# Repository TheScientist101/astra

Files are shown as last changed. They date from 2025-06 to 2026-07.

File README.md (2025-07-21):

<h1 align="center">astra</h1>

   

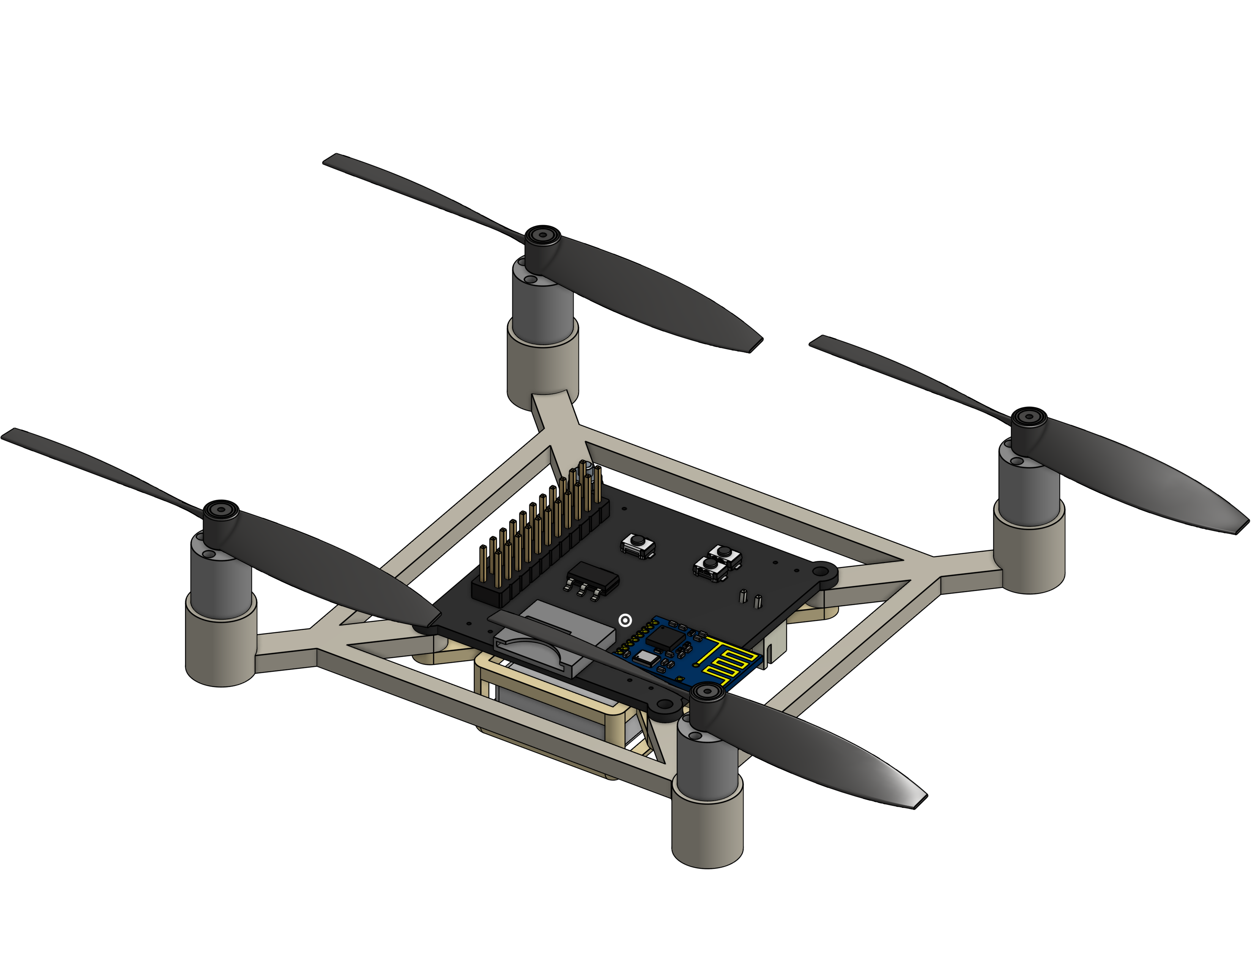
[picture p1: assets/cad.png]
Drone
<h3 align="center">An open source, low cost, extensible brushed drone.</h3>

## What is Astra?

Astra is an `~80mm` brushed quadcopter. It it powered off of a single 1s Li-Po (`4.2V`), and uses four brushed motors.

Astra supports an optional FPV module, and includes a HAT-style pin interface on the flight controller.

We've also designed our own transmitter for Astra. The flight controller and transmitter use an `nRF24` to communicate with low latency.

Every part of Astra was designed from scratch - the flight controller, the transmitter, and the frame.

## Why is Astra?

Siddhant and I both love making things, but we've never made anything that moves before. What cooler of a thing is there that moves than a drone? With air voyage in our control, it would open the gate to even cooler projects, like imagine if you could play laser tag with a drone as your teammate or if you could have a drone that follows you around and takes pictures of you. The possibilities are endless!

That's why we decided to make our drone extensible. To me, modularity is the coolest part of any gadget. It allows you to add new features and capabilities without having to redesign the entire thing. Astra has a HAT-style pin interface called the DUCKDUCKGOOSE (Digital Unified Centralized Kibibit Device Universal Coding Knowledge Generic Operable Objective Service Extensible) Connector on the flight controller, which allows you to add new peripherals and sensors easily.

On the other hand, most drone projects we've seen online are expensive. While Hack Club is dope enough to have a [program that gives us free hardware](https://highway.hackclub.com), it is difficult to find a "DIY" drone that is relatively cheap that flies well. Since we wanted to make sure that our drone was actually good at flying, we decided to remove the onboard camera that we had in our initial design in place of a more traditional FPV system rather than just trying to make our own.

## Cost

All of the components for the drone and can be bought for around `$75`. (See the [`BOM`](./BOM.md) for more details!)

The bulk of this is actually the cost to buy the PCBs and stencil (which is anticipated to be around `$25`). The actual component cost is closer to `$50`.

> Note:
> Adding an FPV system to the drone is relatively costly. The FPV Camera + VTX module costs `$25`, which is actually on the cheaper end for these systems. The total cost with the FPV module is slightly less than `$100` before taxes and other fees.

(for hackclub) Even though the total cost of this drone is under `$150`, we will likely need to have multiple iterations of the PCB before we can get it working right.

## Technical Details

The Flight Controller uses an `STM32H750`. This is a powerful chip with plenty of GPIO pins for peripherals. We plan to implement a software OSD within the H7 for the FPV interface.

PCB files can be found within the `drone/pcb/` folder.

The Flight Controller uses the [betaflight](https://betaflight.com/) firmware. A betaflight config file as well as flashing instructions can be found in the `drone/firmware/` folder

The frame for the FC was designed in Onshape. CAD files can be found in `drone/cad/`;

**Peripherals**:

- `BMI270` - IMU
- `BMP388` - Barometer
- 2 `WS2812B`s
- 2 configurable buttons
- microSD Card Socket
- A 22 pin header for HAT-style extensions. Includes SWD, UART, SPI, I2C, and extra GPIOs.
- An extra UART connector.

The Ground Transmitter uses an `ESP32-C3-SuperMini` (a C3 chip similar to the XIAO that we already have on hand). It features:

- 3 `WS2812B`s
- 2 Joysticks, configured for mode 2 control
- 4 configurable buttons (+2 from the joysticks)

The PCB, firmware, and case for the transmitter can be found in the `controller/` folder

## Pictures

[**Full Schematic PDF**](assets/schematic.pdf)

**Copper Layers:**

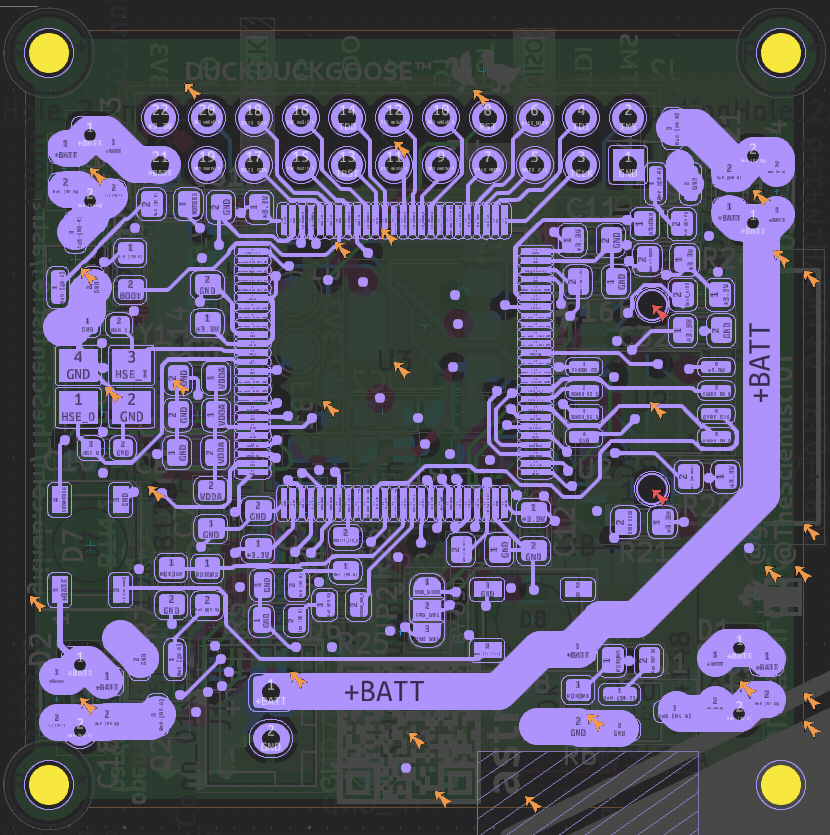
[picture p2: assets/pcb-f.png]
Front Copper Layer
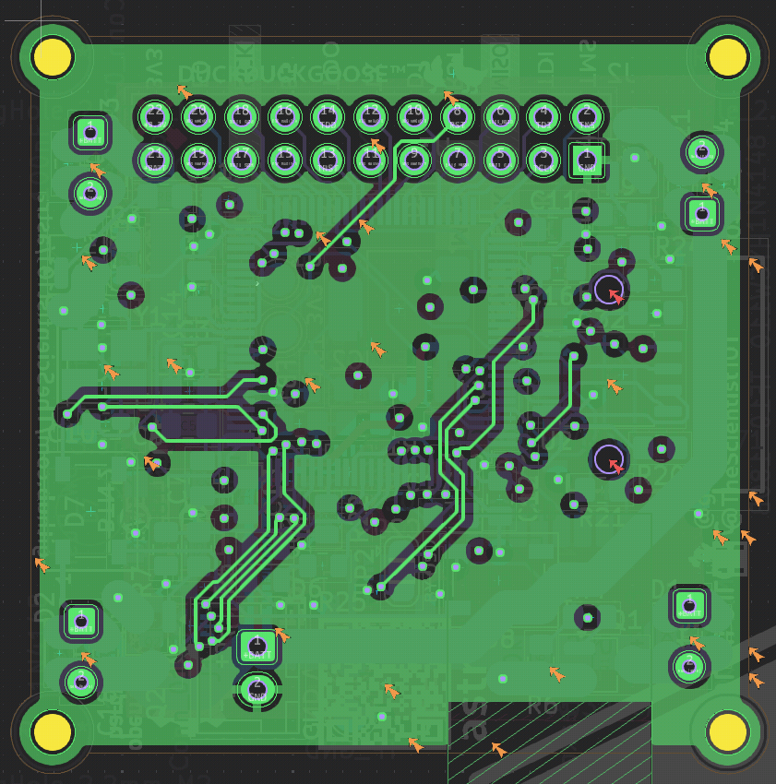
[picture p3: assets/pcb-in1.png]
Inner Layer 1
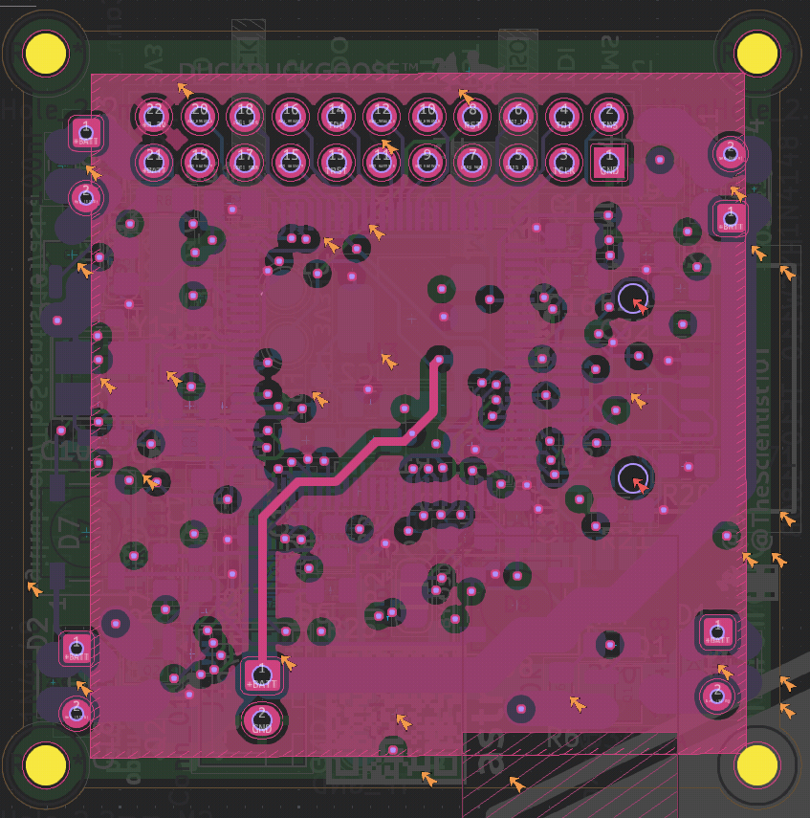
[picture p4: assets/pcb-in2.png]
Inner Layer 2
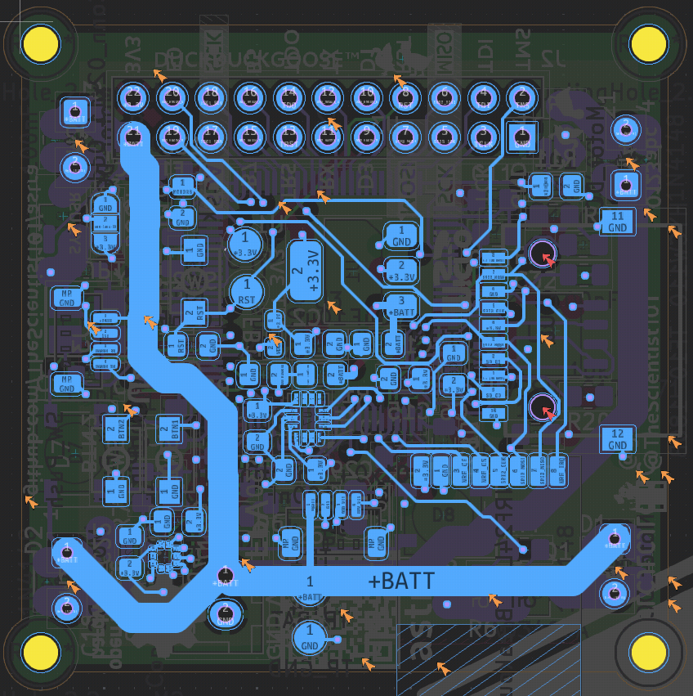
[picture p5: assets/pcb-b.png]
Back Copper Layer
   

**PCB 3D Render:**

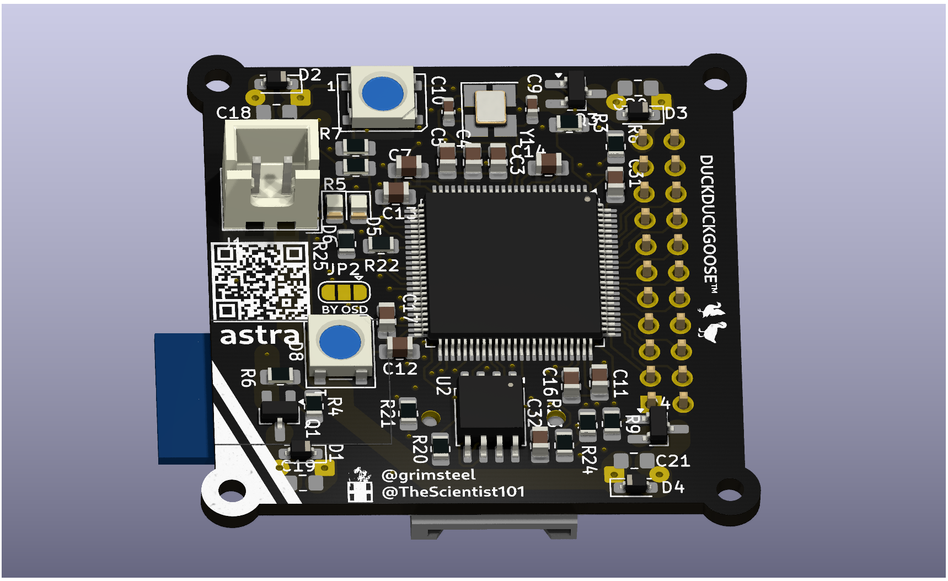
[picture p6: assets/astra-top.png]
top
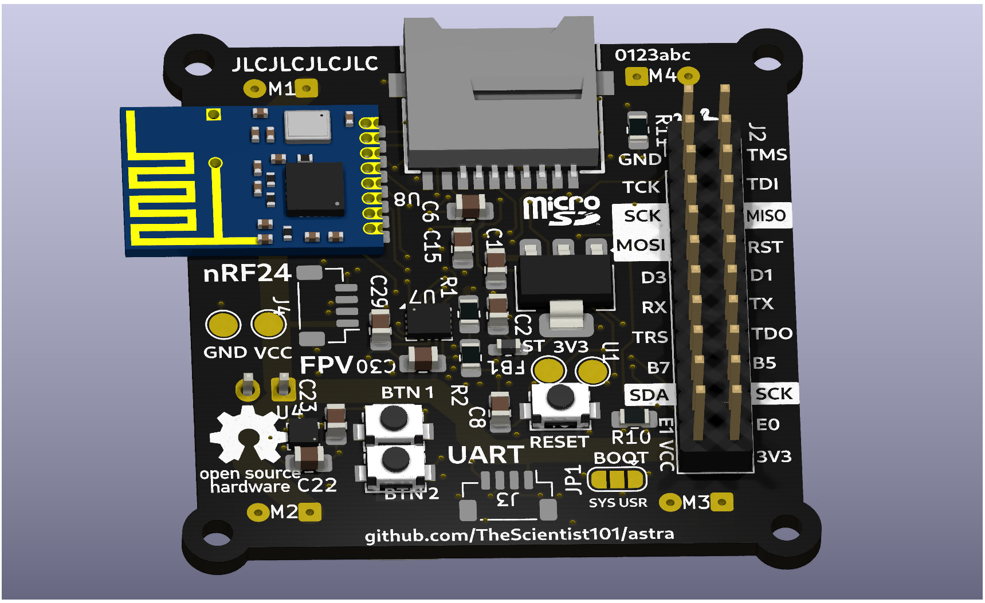
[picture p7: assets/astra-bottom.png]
bottom
 

**Controller PCB Render:**
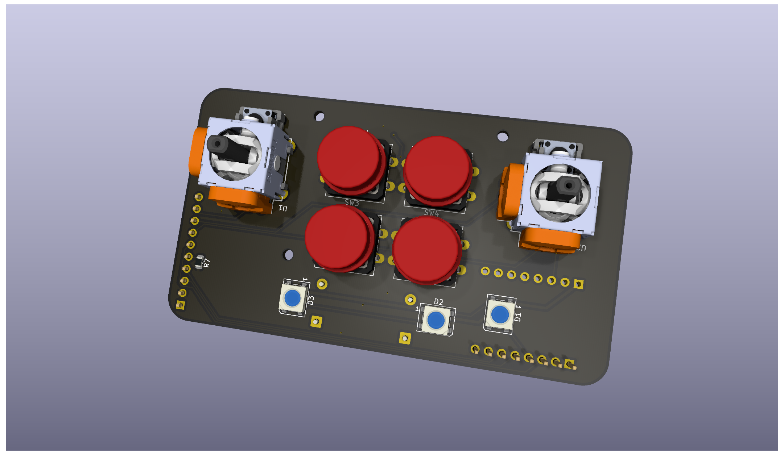
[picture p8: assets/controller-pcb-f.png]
controller pcb front
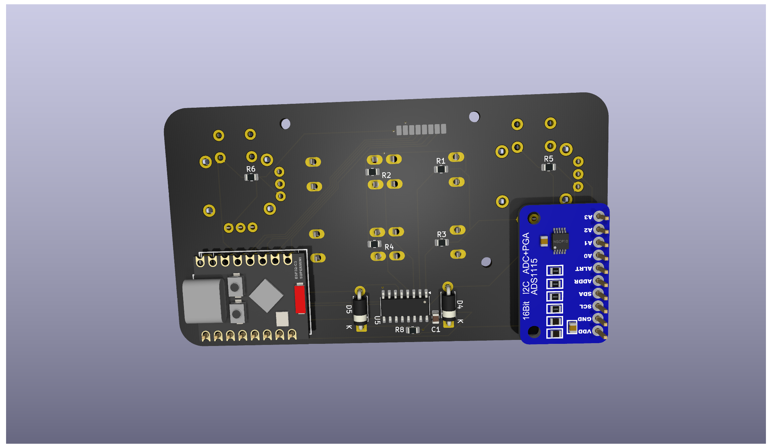
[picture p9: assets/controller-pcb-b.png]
controller pcb back
 

**Controller Assembled Render:**
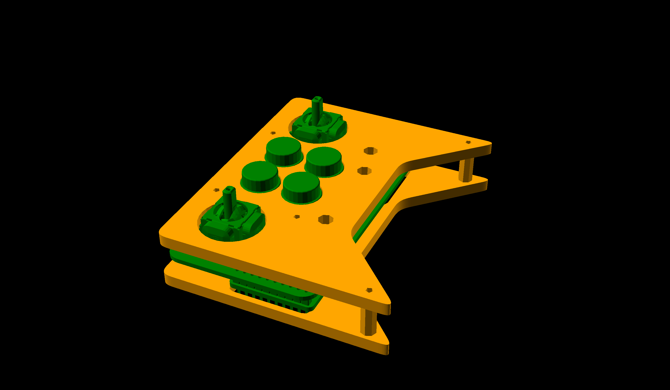
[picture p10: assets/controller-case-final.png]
controller assembled


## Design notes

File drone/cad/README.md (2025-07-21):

# Drone Frame and Battery Holder CAD

The frame and battery holder were designed in Onshape.

[Onshape document](https://cad.onshape.com/documents/556a86aa248807ec932b202d/w/b9d21806660e18ae1fcb018e/e/1638ad71585b5f3276a24b8a)



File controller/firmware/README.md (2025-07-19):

# Ground Controller Firmware

Firmware for the `ESP32-C3-Super Mini` using `esp-idf`.

Drone communication uses the `V202` protocol.

### Credits and Libraries used:

- [`esp-idf-mirf`](https://github.com/nopnop2002/esp-idf-mirf) - nRF24 driver
- [`Flaykz/Wltoys-v202`](https://github.com/Flaykz/Wltoys-v202) - V202 protocol code/TX implementation
- [`betaflight`](https://github.com/betaflight/betaflight/blob/master/src/main/rx/nrf24_v202.c) - Betaflight's V202 implementation (used on the drone)

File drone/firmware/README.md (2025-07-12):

# Building Astra's firmware

Astra's firmware is based on [Betaflight](https://betaflight.com).

We've provided a config in `config.h`. This includes everything except the timer DMA configuration - we need the physical board to figure out this.

Follow these instructions to setup a Betaflight build environment: https://betaflight.com/docs/category/building

## Detailed instructions:

1. Setup Betaflight build environment:
   ```bash
   $ git clone https://github.com/betaflight/betaflight.git
   $ cd betaflight
   $ make arm_sdk_install # if you don't have it installed already
   $ make configs
   ```
   
2. Copy astra config
   ```bash
   $ mkdir -p src/config/configs/ASTRA/
   $ cp /path/to/astra/firmware/config.h src/config/configs/ASTRA/
   ```
   
3. Apply patch to enable nRF24 RX
   ```bash
   $ git apply /path/to/astra/firmware/0001-build-link-NRF24-protocol-sources.patch
   ```
   
4. Build
   ```bash
   $ make ASTRA
   ```

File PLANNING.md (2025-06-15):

# Planning

This is a mirror of our Slack canvas.

## Features

* Parachute
* Solar Panel
    * https://www.aliexpress.us/item/3256808773901038.html
* Toy Ammunition
* Alternate Terrains
* Perching Mechanism
* Autonomous Navigation
    * Auto-Following
        * Using radio signal or camera
        * One follows another
* Mapping using LiDAR or Camera
    * Fastest path
* Radio Integration
* Aerial Laser Tag
* 6“ x 6”

## Budget

Remember to 2x everything at the end

* ESP32-S2 (ESP32-S2-MINI-1U-N4) -  $3.62
    * https://www.digikey.com/en/products/detail/espressif-systems/ESP32-S2-MINI-1U-N4/13180197
* SPI NOR Flash - $0.56
    * BY25Q64ESTIG
* OV3660 or OV2460 - ~$4 - ~10 grams
* Camera Connector - DF40C-30DP-0.4V - $0.81
    * https://www.digikey.com/en/products/detail/hirose-electric-co-ltd/DF40C-30DP-0-4V-51/1969483
* Solder Paste
    * Digikey NC191LT10
    * Aliexpress https://www.aliexpress.us/item/3256806096656294.html $2.98
* PCB - $20-ish - ~10 grams with components except for camera
* Battery - https://www.getfpv.com/sub250-300mah-1s-75c-lipo-battery-5-pcs-a30.html
* IMU - 
* Set of SMD Capacitors/resistors
    * https://www.aliexpress.us/item/3256805970706203.html - 0805 $4.26 for 320pcs
    * https://www.aliexpress.us/item/3256807716137879.html - 0805 $4.17 for 1000pcs (optional)
* AMS1117 3.3
    * Already have
* Propeller
    * https://hackermotors.us/product/gws-prop-3-x-3-hd-set-with-2-pcs/
* Motor ~ 20 grams for all four
    * https://www.aliexpress.us/item/3256802734081484.html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
    * https://excelrc.com/products/betafpv-7x16mm-brushed-motors-19000kv-2cw-2ccw?variant=37534134403259&country=US¤cy=USD&gQT=1
    * https://speedyfpv.com/collections/brushed-motors
    * https://www.amazon.com/Coreless-Brushed-JST-1-25-Connector-Quadcopter/dp/B0CZ6WKVBK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
    * https://www.amazon.com/YoungRC-8520-Coreless-Propeller-Quadcopter/dp/B0BV6P4XYX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—yy_v-cQuJQKe_gynbgR_eZBlEEt8VdUATcRUv22JsLWLuzio.u-IRMGxt2WgfQ5QidPC23q36qNFRAg0-ucyN7Pd-z48&dib_tag=se&keywords=micro+motors&qid=1748056601&s=industrial&sprefix=micro+motors%2Cindustrial%2C121&sr=1-2-spons&sp_csd=d2lkZ2V0TmFtZT1zcF9hdGY&psc=1#averageCustomerReviewsAnchor
* Laser - $6 - ~10 grams
    * https://www.adafruit.com/product/1054
* 3d printing filament ~50 grams

## Motor Math

* Maximum of 150 grams with motors
* at least 75 g of thrust per motor
* 

## Resources

* https://files.seeedstudio.com/wiki/SeeedStudio-XIAO-ESP32S3/res/XIAO_ESP32S3_ExpBoard_v1.0_SCH.pdf
* https://www.unmannedsystemstechnology.com/feature/calculating-how-much-weight-a-drone-can-carry/
* https://www.digikey.com/en/maker/projects/a-step-by-step-guide-to-build-a-low-cost-drone-using-esp32/8afccd0690574bcebfa0d2ad6fd0a391

Measuring battery level: https://vivonomicon.com/2019/10/15/reading-battery-voltage-with-the-stm32s-adc/

OV5640 wiring: https://cdn-learn.adafruit.com/assets/assets/000/118/304/original/adafruit_products_cam_schem.png?1675865865
BMI270 wiring: https://cdn.sparkfun.com/assets/c/a/3/d/f/SparkFun_Qwiic_6DoF_BMI270-Schematic.pdf

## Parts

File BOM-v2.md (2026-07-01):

# Bill of Materials

## General Items and Modules/Breakouts (Amazon + AliExpress)

| Item | Link | Quantity | Total Price | Total Mass on Drone |
|---|---|---|---|---|
| PCB | | 1 | ~$25 | 10g |
| Estimated Tax | - | - | $8.07 | - |
| **Total** | - | - | | |

> The Amazon order total is above $35, so shipping is free.

## PCB Components (LCSC)

_Mass estimate is included in PCB mass estimate_

| Item | Link | Quantity | Total Price | Already Have? |
|---|---|---|---|---|
| ESP32-S3-WROOM-1U-N4R2 | [LCSC](https://www.lcsc.com/product-detail/C3013942.html) | 1 | $4.42 | |
| U.FL Wi-Fi Antenna | [LCSC](https://www.lcsc.com/product-detail/C22467592.html) | 1 | $0.37 | |
| 64 MB NOR Flash: W25Q64JVSSIQ | [LCSC](https://www.lcsc.com/product-detail/NOR-FLASH_Winbond-Elec-W25Q64JVSSIQ_C179171.html?s_z=n_W25Q16JV) | 1 | $0.88 | Yes |
| 32.768 kHz crystal (optional) | [LCSC](https://www.lcsc.com/product-detail/C32346.html) | 1 | $0.87 (5 ct) | |
| TLV1117LV-3.3 | [LCSC](https://lcsc.com/product-detail/Voltage-Regulators-Linear-Low-Drop-Out-LDO-Regulators_JSMSEMI-TLV1117LV33DCYR_C48937499.html) | 1 | $0.54 (for 5) | Yes |
| | | | | |
| A03400A NMOS | [LCSC](https://lcsc.com/product-detail/MOSFETs_UMW-Youtai-Semiconductor-Co-Ltd-AO3400A_C347475.html) | 4 | $0.62 (for 20) | Yes |
| 1N4148 Flyback | [LCSC](https://lcsc.com/product-detail/Switching-Diodes_MDD-Microdiode-Semiconductor-1N4148WS-E_C41371421.html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) | 4 | $0.06 (10 ct) | Yes |
| | | | | |
| 100nF 16V 0805 Capacitor | [LCSC](https://www.lcsc.com/product-detail/Multilayer-Ceramic-Capacitors-MLCC-SMD-SMT_Venkel-C0805X7R160-104KNP_C3865954.html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) | 16 | $0.35 (50 ct) | Yes |
| 1uF 16V 0805 Capacitor | [LCSC](https://www.lcsc.com/product-detail/Multilayer-Ceramic-Capacitors-MLCC-SMD-SMT_Samsung-Electro-Mechanics-CL21B105KOFNNNE_C24123.html) | 2 | $0.21 (20 ct) | Yes |
| 22uF 16V 0805 Capacitor | [LCSC](https://www.lcsc.com/product-detail/C380336.html) | 2 | $0.64 (10 ct) | |
| 5k1 125mW 0603 Resistor | [LCSC](https://www.lcsc.com/product-detail/C23186.html) | 4 | | Yes |
| 1k 125mW 0805 Resistor | [LCSC](https://lcsc.com/product-detail/Chip-Resistor-Surface-Mount_FOJAN-FRC0805J102-TS_C2907295.html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) | 1 | $0.13 (100 ct) | Yes |
| | | | | |
| SD Card Socket | [LCSC](https://lcsc.com/product-detail/SD-Card-Memory-Card-Connector_HOAUC-HYCW110-TF10-180B_C2962030.html) | 1 | $0.54 (10 ct) | Yes |
| SPST Push Button | [LCSC](https://lcsc.com/product-detail/Tactile-Switches_SHOU-HAN-TS342A2P-WZ_C557591.html) | 3 | $0.37 (10 ct) | Yes |
| 0805 Green LED | [LCSC](https://lcsc.com/product-detail/LED-Indication-Discrete_Yongyu-Photoelectric-SZYY0805G1_C19712537.html) | 1 | $0.27 (50 ct) | Yes |
| WS2812B | [LCSC](https://lcsc.com/product-detail/RGB-LEDs-Built-in-IC_XINGLIGHT-XL-5050RGBC-WS2812B-S_C22461793.html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) | 3 | $0.53 (20 ct) | Yes |
| | | | | |
| BMI270 IMU | [LCSC](https://www.lcsc.com/product-detail/Accelerometers_Bosch-Sensortec-BMI270_C2836813.html?s_z=n_BMI270) | 1 | $2.41 (other suppliers) | Soldered |
| QMC5883P Compass | [LCSC](https://www.lcsc.com/product-detail/C2847467.html) | 1 | $1.53 | |
| HBP401G101S6 Barometer | [LCSC](https://www.lcsc.com/product-detail/C49229983.html) | 1 | $0.89 | |
| ATGM332D GPS | [LCSC](https://www.lcsc.com/product-detail/C3037611.html) | 1 | $1.80 | |
| AT2659 LNA | [LCSC](https://www.lcsc.com/product-detail/C883443.html) | 1 | $0.43 (5 ct) | |
| 470 pF 0603 Capacitor | [LCSC](https://www.lcsc.com/product-detail/C3893316.html) | 1 | $0.11 (50 ct) | |
| 6.8 nH 0603 Inductor | [LCSC](https://www.lcsc.com/product-detail/C55067207.html) | 1 | $0.23 (50 ct) | |
| GNSS Patch Antenna | [LCSC](https://www.lcsc.com/product-detail/C6569550.html) | 1 | $0.66 | |
| | | | | |
| 24P FPC Cable 5cm 1mm | [LCSC](https://www.lcsc.com/product-detail/C2857608.html) | 1 | $0.39 (5 ct) | |
| 24P FPC Connector 1mm | [LCSC](https://www.lcsc.com/product-detail/C262726.html) | 2 | $0.80 (5 ct) | |
| USB-C Receptacle 14 Pin THT | [LCSC](https://www.lcsc.com/product-detail/C168704.html) | 1 | $0.41 | |
| | | | | |
| LCSC shipping | N/A | N/A | $9.45 | |
| **Total** | - | - | ? | |

<!--
| ESP32-S3-WROOM-1U-N4 | [DigiKey](https://www.digikey.com/en/products/detail/espressif-systems/ESP32-S3-WROOM-1U-N4/16162640) [LCSC](https://www.aliexpress.us/item/3256806096656294.html) | 1 | $3.61 + $4.99 | - |
| BetaFPV 1102 Brushless Motors | [Amazon](https://www.amazon.com/BETAFPV-18000KV-Brushless-Motor-Meteor75/dp/B0834P2LSY) | 4 | $45.99 | 11.2g |
-->

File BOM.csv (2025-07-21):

Name | Link | Quantity | Total Price
Drone PCB + Drone Stencil + Controller PCB + Shipping | N/A | 1 | $30.00
NRF24L01 Breakout (SMD24L01) | https://www.aliexpress.us/item/3256805889378019.html | 2 | $2.01
ADS1115 ADC | https://www.aliexpress.us/item/2251832125341942.html | 1 | $1.61
SMD Solder Paste | https://www.aliexpress.us/item/3256807158914612.html | 1 | $3.36
4 pin JST SH-1.0 Connector | https://www.aliexpress.us/item/3256805841019654.html | 1 | $1.78
2 pin JST MX-2.0 Connector | https://www.aliexpress.us/item/3256806058517035.html | 1 | $3.30
M2 Screws + Nuts | https://www.aliexpress.us/item/3256804647352410.html | 6 | $5.26
Li-Po Battery (380mAh, 25C) | https://www.amazon.com/URGENEX-380mAh-Battery-Charger-Controller/dp/B08DD5MTKM | 1 | $13.99
YoungRC 8520 Coreless Motor | https://www.amazon.com/YoungRC-8520-Coreless-Propeller-Quadcopter/dp/B0BV6P4XYX | 4 | $11.99
FPV Camera + Transmitter | https://www.amazon.com/Wolfwhoop-5-8GHz-Transmitter-Interface-Quadcopter/dp/B073J61SSQ | 1 | $25.99
Estimated Amazon + Ali Tax | - | N/A | $8.19
3D Printed Frame +Case | N/A | 1 | $0.00
64 MB NOR Flash: W25Q64JVSSIQ | https://www.lcsc.com/product-detail/NOR-FLASH_Winbond-Elec-W25Q64JVSSIQ_C179171.html | 1 | $2.32
A03400A NMOS | https://lcsc.com/product-detail/MOSFETs_UMW-Youtai-Semiconductor-Co-Ltd-AO3400A_C347475.html | 4 | $0.62
BMI270 IMU | https://www.lcsc.com/product-detail/Accelerometers_Bosch-Sensortec-BMI270_C2836813.html | 1 | $0.46
STM32H750XBH6 | https://www.lcsc.com/product-detail/Microcontrollers-MCU-MPU-SOC_STMicroelectronics-STM32H750XBH6_C405932.html | 1 | $6.40
25 MHz Crystal (optional, but good) | https://lcsc.com/product-detail/Crystals_Shenzhen-SCTF-Elec-SX3B25-000F1010F30_C2901684.html | 1 | $0.39
TLV1117LV-3.3 | https://www.lcsc.com/product-detail/Voltage-Regulators-Linear-Low-Drop-Out-LDO-Regulators_Texas-Instruments-TLV1117LV33DCYR_C15578.html | 1 | $1.02
FCM1608KF-601T05 Ferrite Beads | https://www.lcsc.com/product-detail/Ferrite-Beads_TAI-TECH-FCM1608KF-601T05_C133937.html | 1 | $0.18
100nF 16V 0805 Capacitor | https://www.lcsc.com/product-detail/Multilayer-Ceramic-Capacitors-MLCC-SMD-SMT_Venkel-C0805X7R160-104KNP_C3865954.html | 22 | $0.35
1uF 16V 0805 Capacitor | https://www.lcsc.com/product-detail/Multilayer-Ceramic-Capacitors-MLCC-SMD-SMT_Samsung-Electro-Mechanics-CL21B105KOFNNNE_C24123.html | 2 | $0.21
10uF 16V 0805 Capacitor | https://www.lcsc.com/product-detail/Multilayer-Ceramic-Capacitors-MLCC-SMD-SMT_Samsung-Electro-Mechanics-CL21A106KOQNNNE_C1713.html | 3 | $0.18
3.9pF 50V 0603 Capacitor | https://www.lcsc.com/product-detail/Multilayer-Ceramic-Capacitors-MLCC-SMD-SMT_Walsin-Tech-Corp-MT18N3R9C500CT_C908519.html | 2 | $0.05
4.7uF 25V 0805 Capacitor | https://www.lcsc.com/product-detail/Multilayer-Ceramic-Capacitors-MLCC-SMD-SMT_Samsung-Electro-Mechanics-CL21A475KAQNNNE_C1779.html | 1 | $0.23
200nF 50V 0805 Capacitor | https://www.lcsc.com/product-detail/Multilayer-Ceramic-Capacitors-MLCC-SMD-SMT_CCTC-TCC0805X7R204K500DT_C344170.html | 2 | $0.48
1N4148 Flyback | https://lcsc.com/product-detail/Switching-Diodes_MDD-Microdiode-Semiconductor-1N4148WS-E_C41371421.html | 4 | $0.06
100k 125mW 0805 Resistor | https://www.lcsc.com/product-detail/Chip-Resistor-Surface-Mount_FOJAN-FRC0805J104-TS_C2907293.html | 2 | $0.13
10k 125mW 0805 Resistor | https://www.lcsc.com/product-detail/Chip-Resistor-Surface-Mount_FOJAN-FRC0805J103TS_C2930231.html | 17 | $0.11
220 125mW 0805 Resistor | https://www.lcsc.com/product-detail/Chip-Resistor-Surface-Mount_FOJAN-FRC0805J221-TS_C2933537.html | 4 | $0.13
1k 125mW 0805 Resistor | https://lcsc.com/product-detail/Chip-Resistor-Surface-Mount_FOJAN-FRC0805J102-TS_C2907295.html | 2 | $0.13
SD Card Socket | https://lcsc.com/product-detail/SD-Card-Memory-Card-Connector_HOAUC-HYCW110-TF10-180B_C2962030.html | 1 | $0.54
SPST Push Button | https://lcsc.com/product-detail/Tactile-Switches_SHOU-HAN-TS342A2P-WZ_C557591.html | 3 | $0.37
0805 Green LED | https://lcsc.com/product-detail/LED-Indication-Discrete_Yongyu-Photoelectric-SZYY0805G1_C19712537.html | 2 | $0.27
WS2812B | https://lcsc.com/product-detail/RGB-LEDs-Built-in-IC_XINGLIGHT-XL-5050RGBC-WS2812B-S_C22461793.html | 5 | $0.53
BMP388 Barometer | https://lcsc.com/product-detail/Pressure-Sensors_Bosch-BMP388_C779278.html?s_z=n_BMP388 | 1 | $1.25
SN74HC148 Priority Encoder | https://lcsc.com/product-detail/Signal-Switches-Multiplexers-Decoders_lingxingic-SN74HC148DR-LX_C41413103.html | 1 | $0.74
LCSC shipping | N/A | N/A | $9.30
1N5819 Schottky | N/A | 2 | $0.00
ESP32-C3 Super Mini | N/A | 1 | $0.00
Hall effect Joystick | N/A | 2 | $0.00
12mm Push Button | N/A | 4 | $0.00
Total | N/A | N/A | $133.93

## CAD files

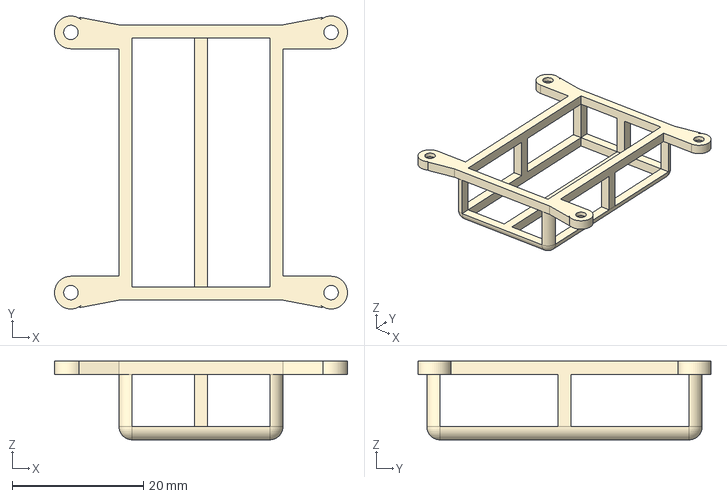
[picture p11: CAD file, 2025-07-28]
drone/cad/battery-mount.step
44.7 x 44.7 x 12.0 mm

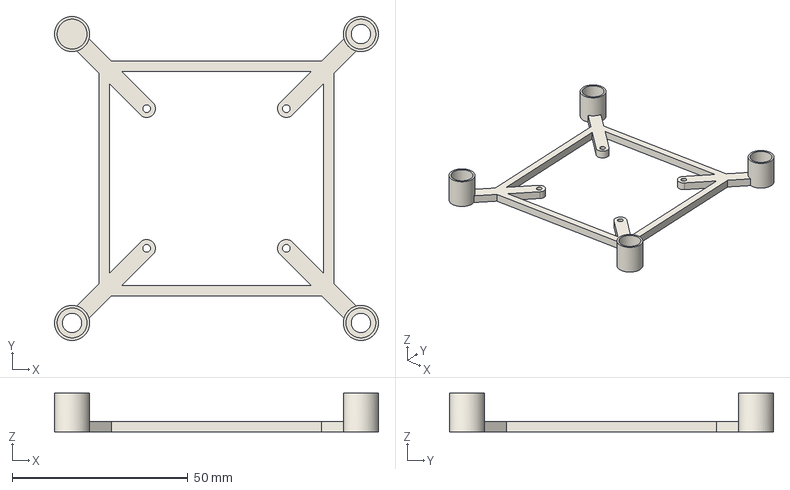
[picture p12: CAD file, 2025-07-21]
drone/cad/frame.step
92.1 x 92.1 x 11.0 mm

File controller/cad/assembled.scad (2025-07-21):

use <basics.scad>
use <case_bottom.scad>
use <case_top.scad>

height = 4;

color("orange") translate([0, 0, 8]) {
    case_top(height=height);

    // spacers
    translate([-21.06, -18.4, -height / 2 - 0.1 - 2.5]) spacer(height=5);
    translate([-21.06, 19.74, -height / 2 - 0.1 - 2.5]) spacer(height=5);
    translate([8.44, -20.39, -height / 2 - 0.1 - 2.5]) spacer(height=5);
}
color("green") rotate([0, 0, 90]) import("./components/pcb.stl");
color("orange") translate([0, 0, -7]) {
    case_bottom(height=height);

    // spacers
    translate([-21.06, -18.4, height / 2 + 0.1 + 2.5]) spacer(height=5);
    translate([-21.06, 19.74, height / 2 + 0.1 + 2.5]) spacer(height=5);
    translate([8.44, -20.39, height / 2 + 0.1 + 2.5]) spacer(height=5);
}

color("orange") translate([42, -42.5, 0.5]) spacer(height=10.9);
color("orange") translate([42, 42.5, 0.5]) spacer(height=10.9);

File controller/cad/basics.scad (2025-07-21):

include <BOSL2/std.scad>

module base_shape(height=4) {
    rounded_prism(rect([52, 92], chamfer=[-25, 0, 0, -25]), height=height, joint_sides=5);
}

module spacer(height, outer_radius=2.5, inner_radius=1.1) {
    difference() {
        cylinder(r=outer_radius, h=height, center=true);
        cylinder(r=inner_radius, h=height + 0.1, center=true);
    }
}

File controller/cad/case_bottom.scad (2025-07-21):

include <BOSL2/std.scad>
use <basics.scad>

module case_bottom(height=4) {
    difference() {
        base_shape(height=height);
        translate([13.76, 28.18, 0]) cuboid([18.6, 24.6, height + 1], rounding=2, except=[TOP, BOTTOM]);
        translate([10, -35, 0]) cuboid([27, 18, height + 1], rounding=2, except=[TOP, BOTTOM]);
        
        translate([-21.06, -18.4, 0]) cylinder(r=1.1, h=height + 1, center=true);
        translate([-21.06, 19.74, 0]) cylinder(r=1.1, h=height + 1, center=true);
        translate([8.44, -20.39, 0]) cylinder(r=1.1, h=height + 1, center=true);
        translate([-21.06, -18.4, -2.5/2]) cylinder(r=3, h=2.5, center=true);
        translate([-21.06, 19.74, -2.5/2]) cylinder(r=3, h=2.5, center=true);
        translate([8.44, -20.39, -2.5/2]) cylinder(r=3, h=2.5, center=true);

        translate([42, -42.5, 0]) cylinder(r=1.1, h=height + 1, center=true);
        translate([42, 42.5, 0]) cylinder(r=1.1, h=height + 1, center=true);
        translate([42, -42.5, -2.5/2]) cylinder(r=3, h=2.5, center=true);
        translate([42, 42.5, -2.5/2]) cylinder(r=3, h=2.5, center=true);
    }
}

translate([0, 0, -7]) case_bottom();
color("green") rotate([0, 0, 90]) import("./components/pcb.stl");

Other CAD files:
controller/cad/case_top.scad
controller/cad/spacer.scad

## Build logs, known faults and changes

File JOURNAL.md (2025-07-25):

---
title: "astra"
author: "Urjith Mishra (@TheScientist101) and Siddhant Kameswar (@grimsteel)"
description: "Astra is an open source, low cost, extensible brushed drone."
created_at: "2025-05-23"
---

### Total hours:

- Urjith Mishra: 36
- Siddhant Kameswar: 55

# May 23rd:

Urjith + Siddhant

**Hours spent: 3 each (huddle)**

We decided the initial drone features.

We plan on making a laser tag drone:

- Each player will control their own drone. (We'll be manufacturing two for this.)
- The objective of the game will be for the drones to find and tag each other using the attached remote controllable laser and IR sensors.

Other features include semi-autonomous navigation as well as a camera for photos/FPV.

Our main concern is the thrust and the weight of the drone.

This is what we spent the majority of the time figuring out, but we learned a lot about aerodynamics.

We decided on an initial BOM, which is included in our [Full planning document](./PLANNING.md)

# June 4th:

Urjith + Siddhant

**Hours spent: 3.5 each (huddle)**

We did extensive research into components and created a more thorough [BOM](./BOM.md)

- We decided to use an STM32H7 microcontroller because of it's increased processing capabilities compared to the ESP32 and its compatibility with camera protocols, specifically DCMI.
- We decided on a brushless motor and propellers to allow us a total weight of 80 grams.
- We picked a camera model and did some research into the supporting components.
- We did some initial calculations regarding the weight of the drone components using [ecalc](https://ecalc.ch).
- We did some research on batteries, but that honestly bamboozled us more, so the battery is very much TBD.

We also decided to deprioritize laser tag, instead focusing on a modular design.

We are approaching our budget pretty quickly... We must keep in mind the cost of iterations and small things such as solder stencil.

# June 10th

Urjith + Siddhant

**Hours spent: 2.5 each (huddle)**

We finished up our component research. ([BOM](./BOM.md))

- After considering the components and precision needed (ESC) to properly control a brushless motor, we decided to use a brushed motor instead of a brushless motor to decrease the overall complexity of the project
- We did some research regarding motor control (MOSFETS) and chose the components for this
- We also picked the remaining miscellaneous components on the PCB (Flash, IMU)
- We're finally ready to start the PCB design!
- We made a rough sketch of the device, which is shown below:

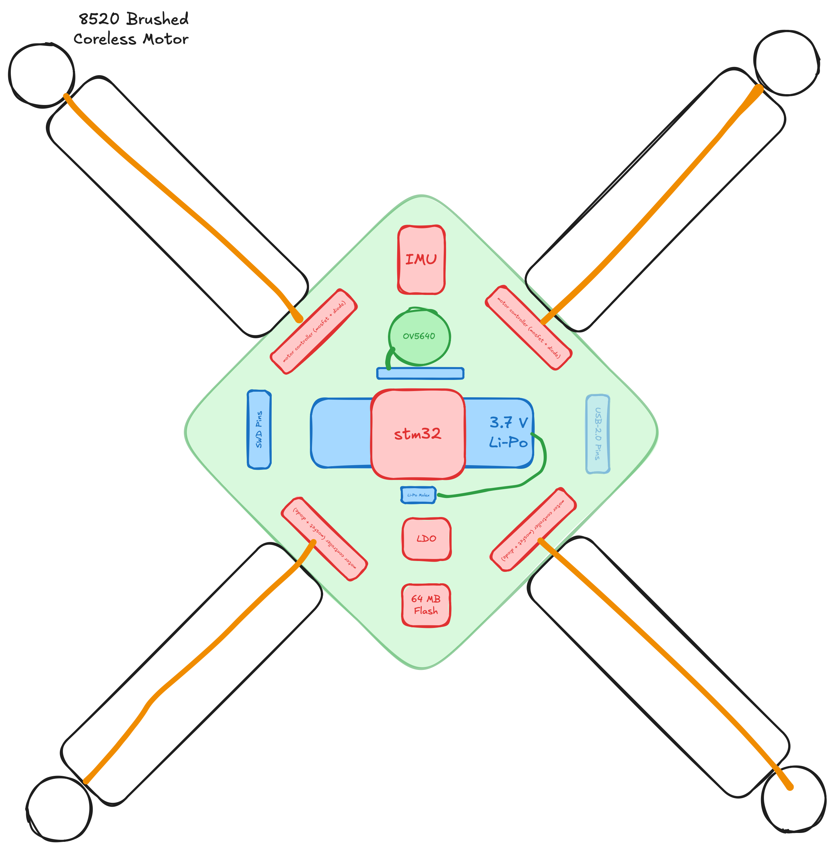
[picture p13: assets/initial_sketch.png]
Sketch


# June 10th

Urjith + Siddhant

**Hours spent: 2 each (huddle)**

We started the initial schematic design

- We created multiple subsheets to make collaboration easier (and to reduce merge conflicts)
- We did some initial wiring for the STM32, flash, and power supply

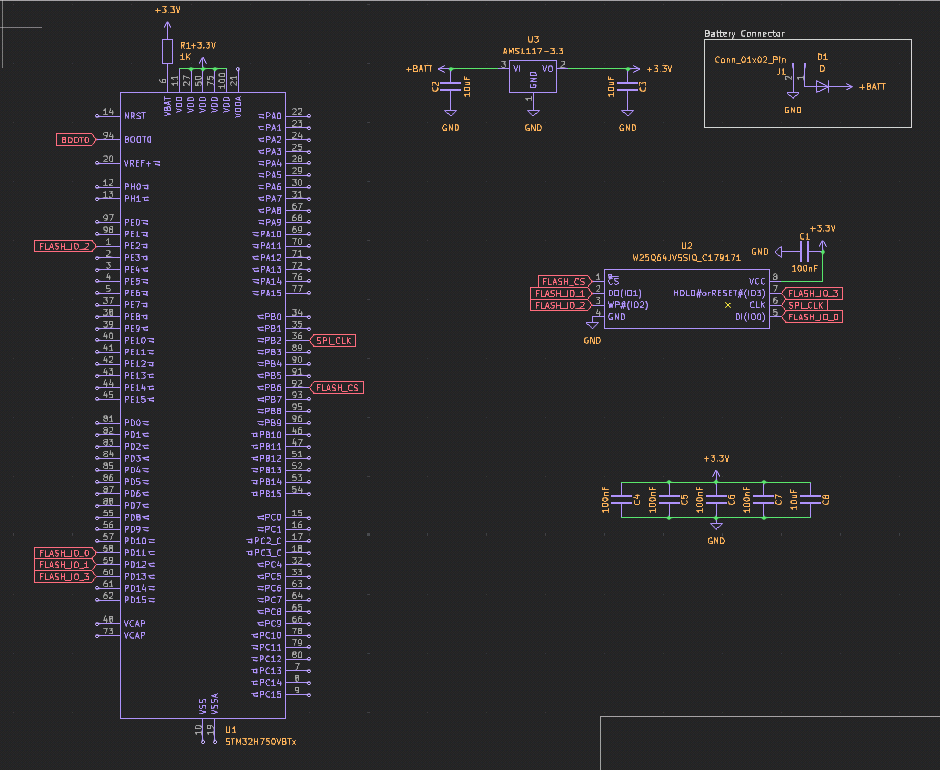
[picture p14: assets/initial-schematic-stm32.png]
STM32 Schematic


# June 11th

Urjith + Siddhant

**Hours spent: 1 each (huddle)**

We continued the schematic design

- We added more power stuff for the STM32.
- We looked more into STM32 datasheet to figure out what was needed and what capacitor values to use.
- Throughout the day, we did some research into other drone projects to see how they did their schematics and what components they used. (not logged for time, but thought this was worth mentioning)

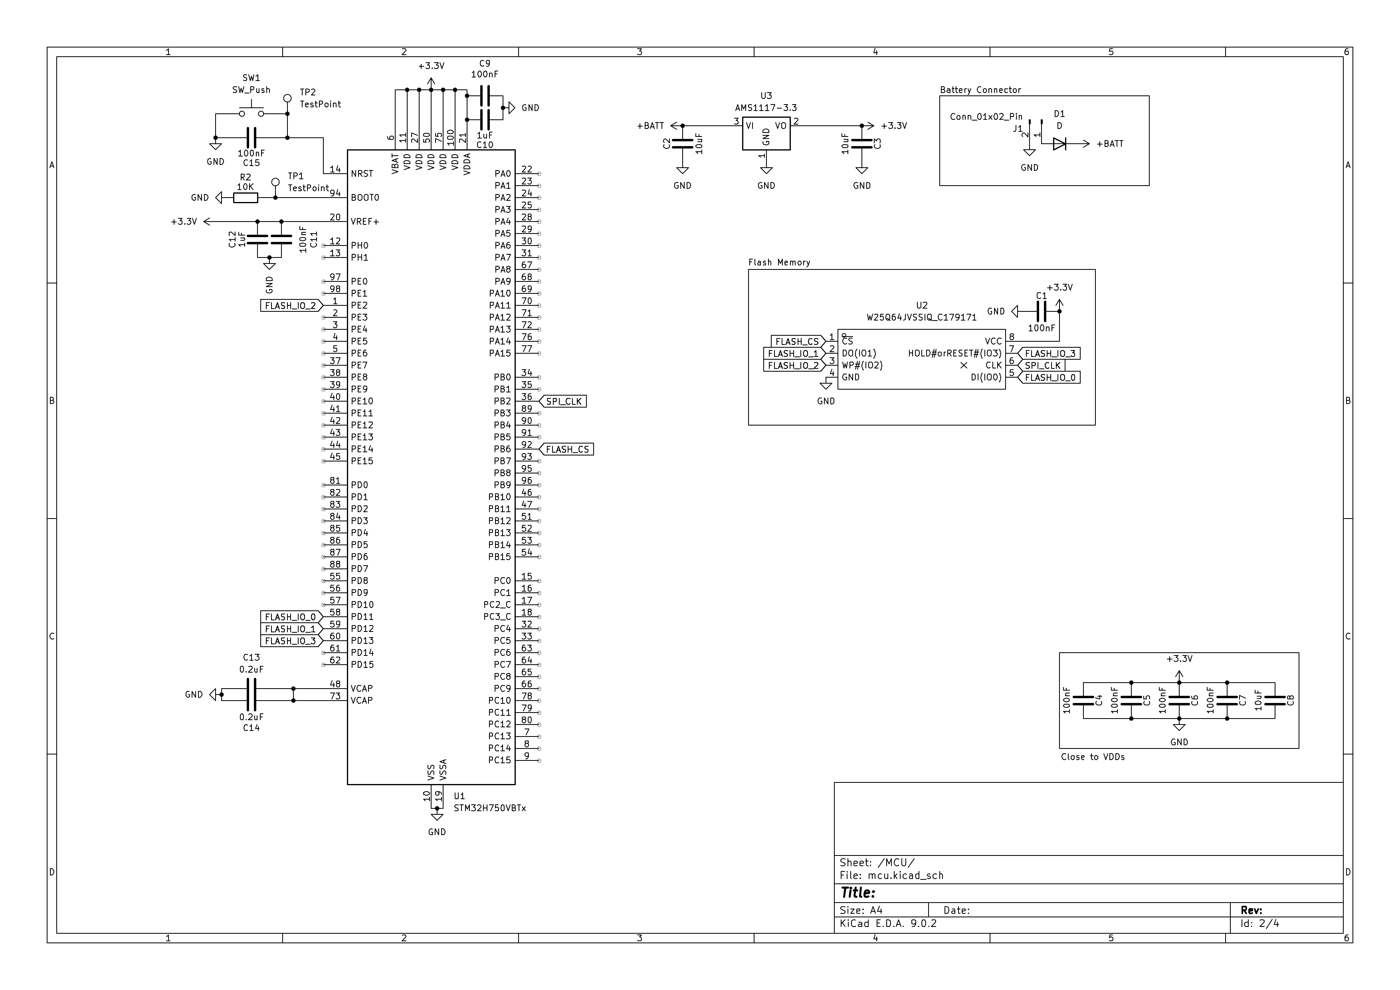
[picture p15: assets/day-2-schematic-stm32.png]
STM32 Schematic


# June 12th

Urjith + Siddhant
**Hours spent: 2 each (huddle)**

We continued the schematic design

- Siddhant worked on the motor control MOSFET things.
- He researched which MOSFETs were capable of handling the current and voltage we needed.
- He researched better voltage regulators.
- Urjith finished up the basic STM32 wiring.
- He researched which transceiver to use for the drone. We decided to use the NRF24L01+ transceiver because of its low cost and good range.
- He started wiring the transceiver to the STM32.

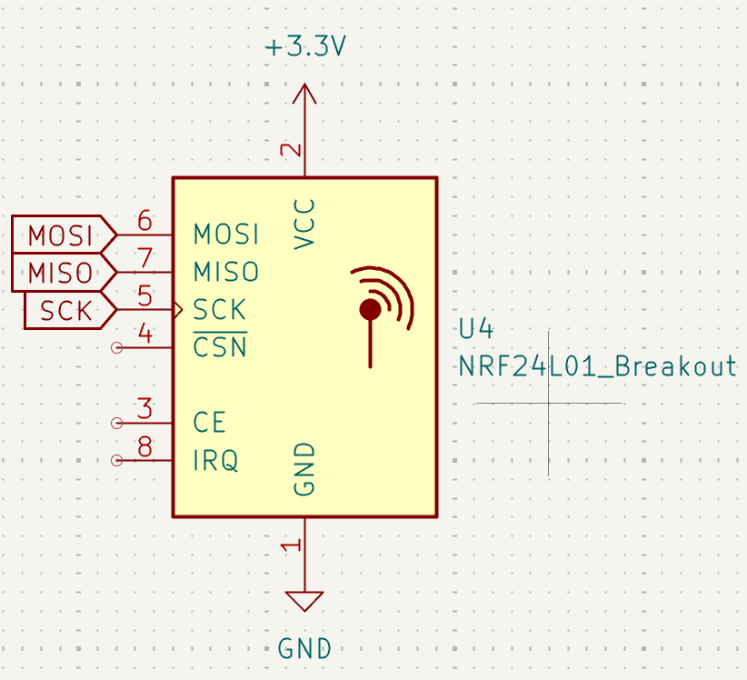
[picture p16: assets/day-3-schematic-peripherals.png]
Peripherals Schematic
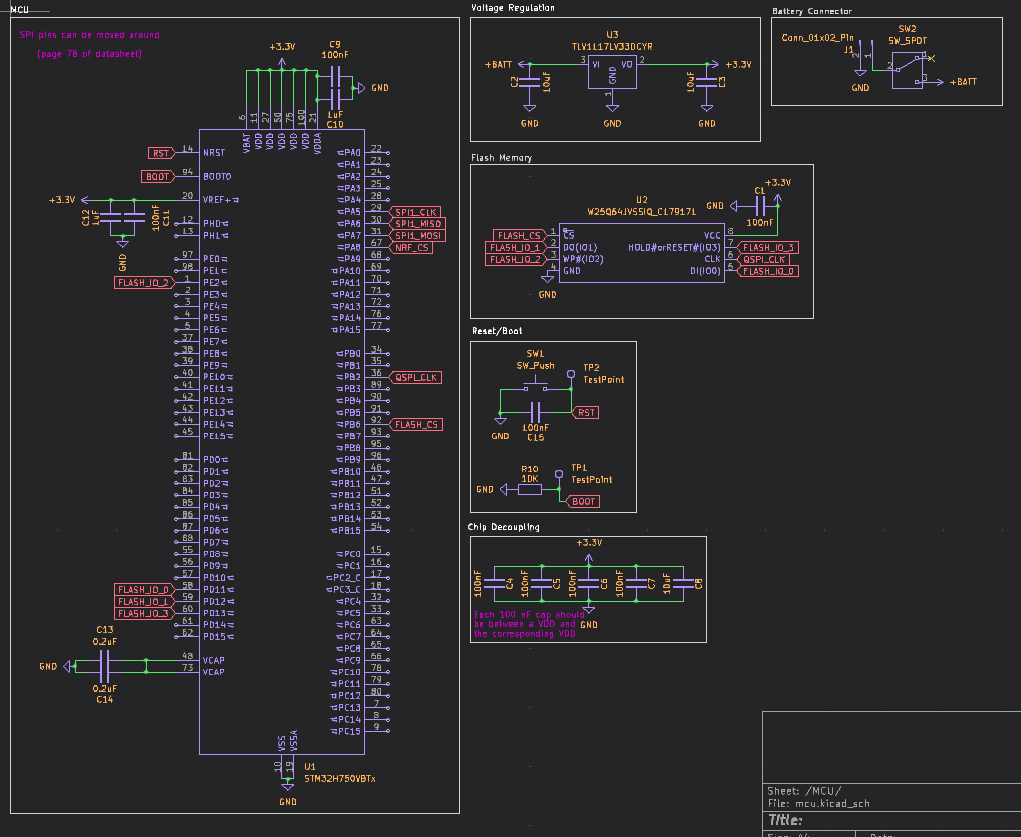
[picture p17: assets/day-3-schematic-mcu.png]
MCU Schematic
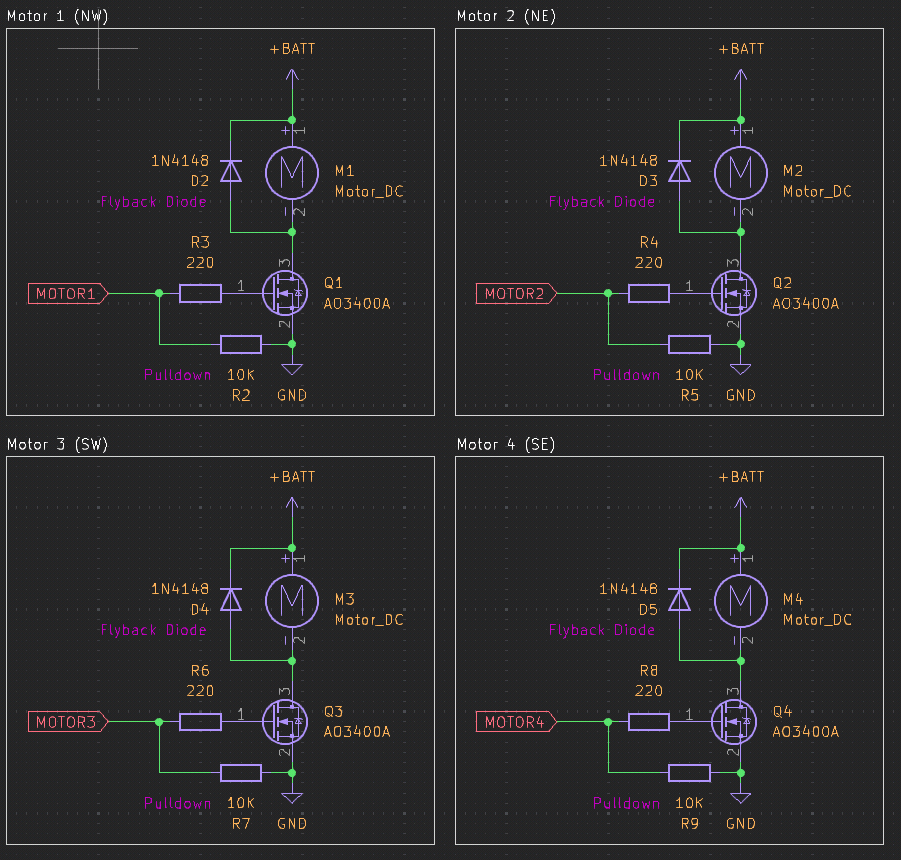
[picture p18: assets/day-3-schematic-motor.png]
Motor Controller Schematic
  

# June 13th-14th

Siddhant

**Hours spent: 5**

I added almost all of the peripherals to the schematic:

- **JTAG connector for debugging** - this one was relatively simple as it's just a bunch of connections
- **NRF Wireless Chip** - Urjith had started this already, so I just finished the wiring. I decided to use the SPI2 peripheral instead of SPI1 (more on this below)
- **OV5640 Camera** - This was definitely the most complex. The Adafruit breakout board for the OV5640 was a very helpful reference for figuring out the wiring and components/pullups needed. I had to use 2 additional LDOs as well. I connected this to the STM32's DCMI interface as well as the I2C1 peripheral.
- **IMU** - This was relatively simple. I used a Sparkfun breakout board as a reference, and connected it to the I2C2 peripheral. I'm not sure whether multiple I2C subs can exist on the same peripheral, but we have enough pins on the STM32 to just use another.

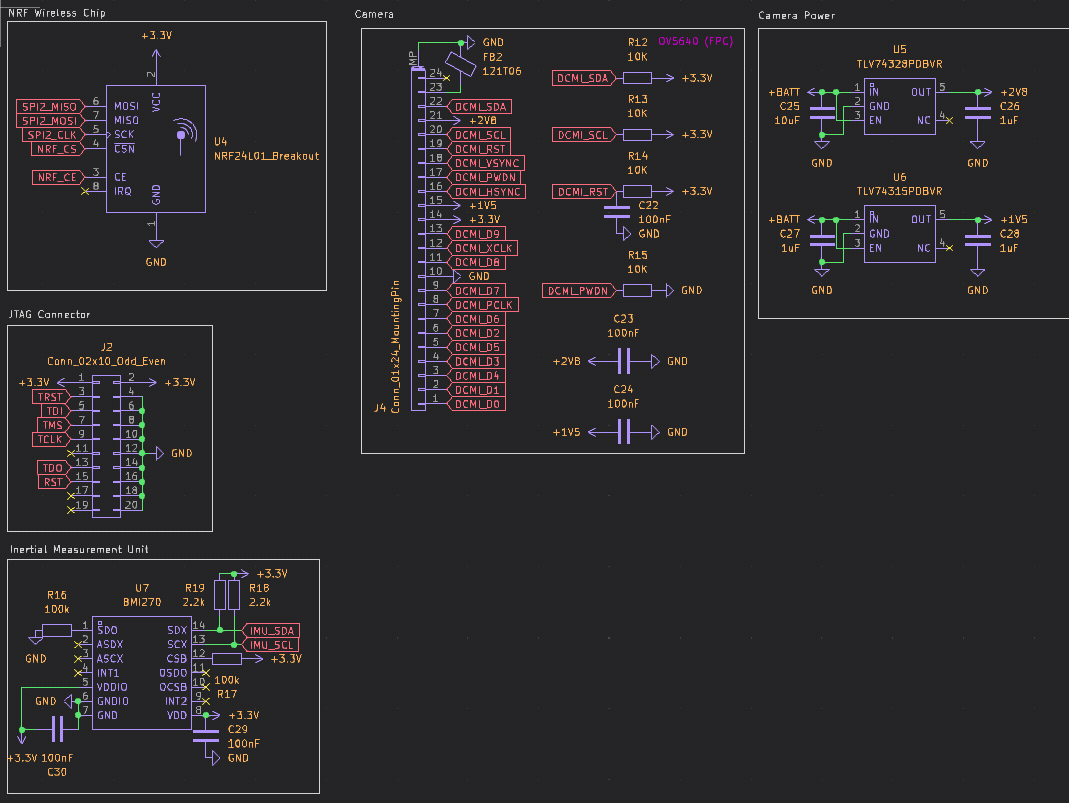
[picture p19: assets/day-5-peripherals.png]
Peripherals


I also added a voltage divider to the battery so we can measure its voltage (using ADC1)

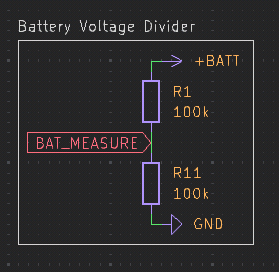
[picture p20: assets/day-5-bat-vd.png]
Battery


I decided to use an external 25 MHz crystal (recommended by the datasheet)

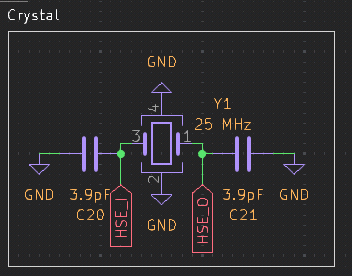
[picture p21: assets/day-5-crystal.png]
rocket


The hardest part of all of this was figuring out where to connect everything to the STM32. It's not like an ESP32 which has a GPIO matrix, which means there are specific pins for SPI and I2C and the other peripherals.

The STM32CubeMX software was a huge help with this. It helped me pick which pins to use to avoid conflicts.

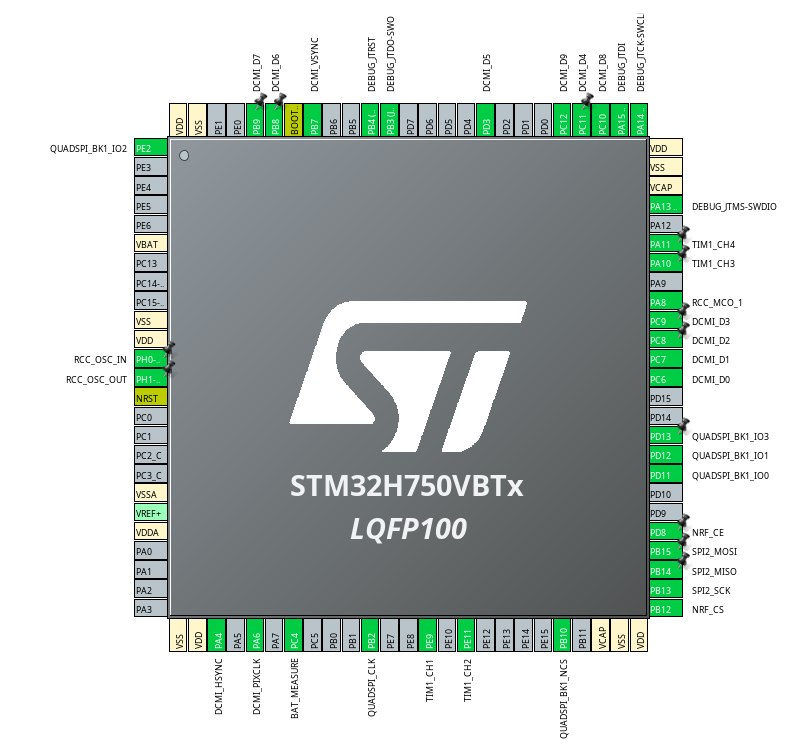
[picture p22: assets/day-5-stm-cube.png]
cube


With this configuration, SPI1 is actually unusable, which is why I used SPI2.

Here's the resulting schematic:

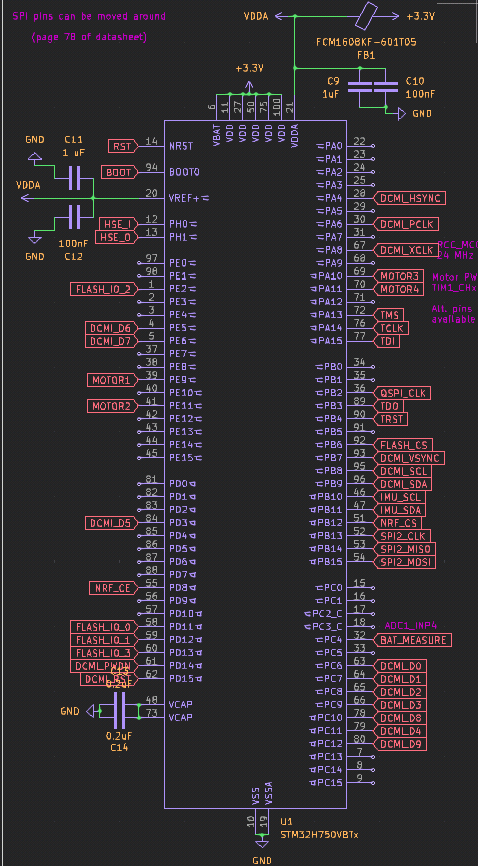
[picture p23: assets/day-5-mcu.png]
mcu


I did end up altering some of the power circuitry again (ferrite bead between VDDA/VREF and +3.3V)

# June 20th

Urjith + Siddhant
**Hours spent: 2 each (huddle)**

Siddhant started routing the PCB. He finalized the placement of most of the components and started routing the power traces. To improve signal quality, we decided to use four layers instead of two, and we will need to move the components around and re-route the PCB.

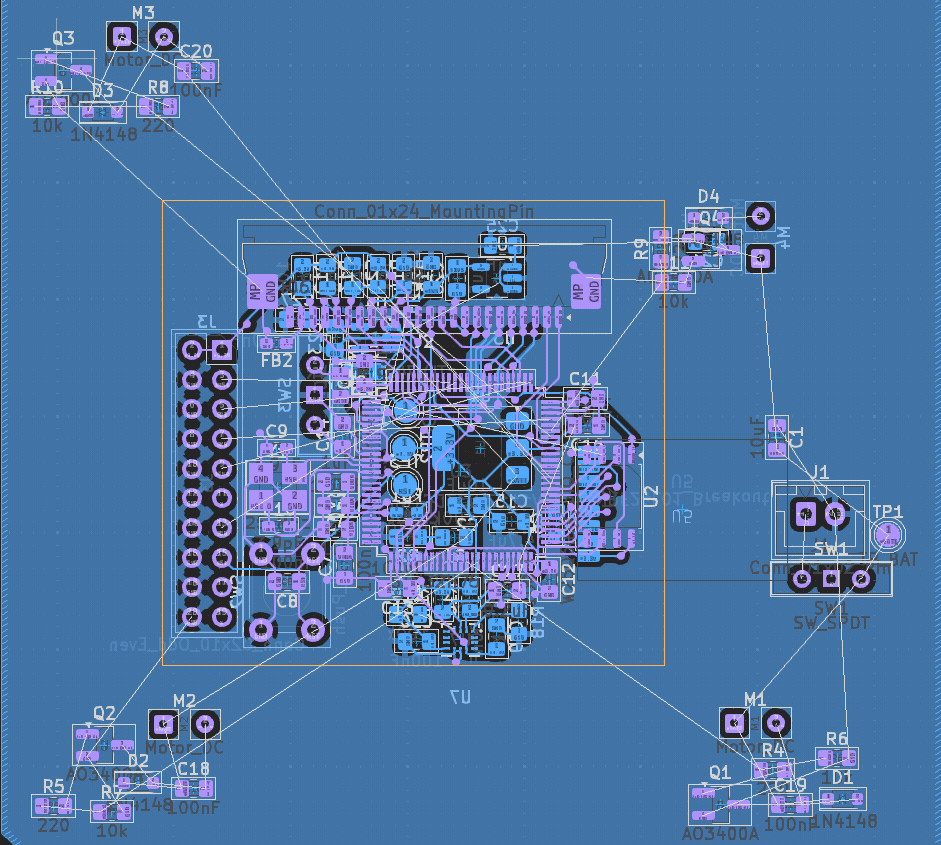
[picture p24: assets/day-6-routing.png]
PCB Placement


Urjith added the micro secure digital card interface socket connector to the schematic. We researched the microSD specification and the necessity for pull-up resistors on the data lines.

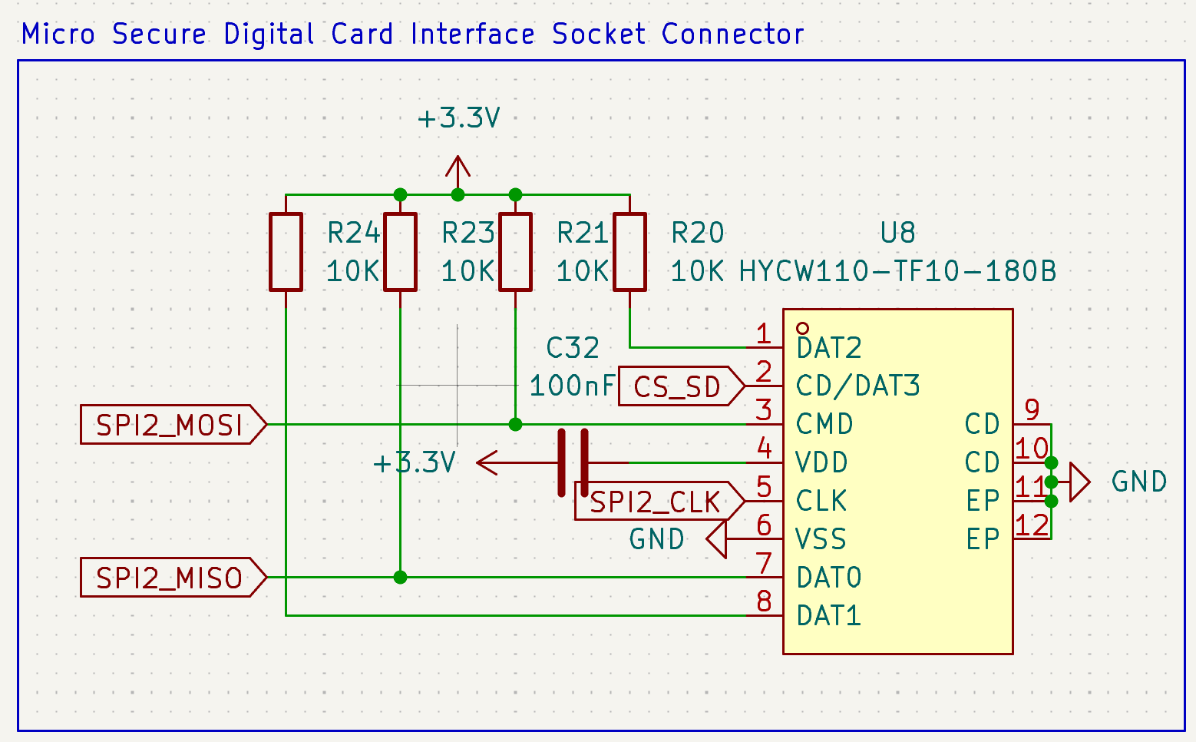
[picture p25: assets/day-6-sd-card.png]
SD Card Schematic


We still need to add a HAT interface connector socket for extensibility and modularity, but we will do that later.

# June 21st-30th

Siddhant

**Hours spent: 5**

Both of us have been pretty busy this past week, but I've been gradually routing the new PCB.

We switched to 4 layers for better signal quality and easier routing, so we had to pretty much start from scratch.

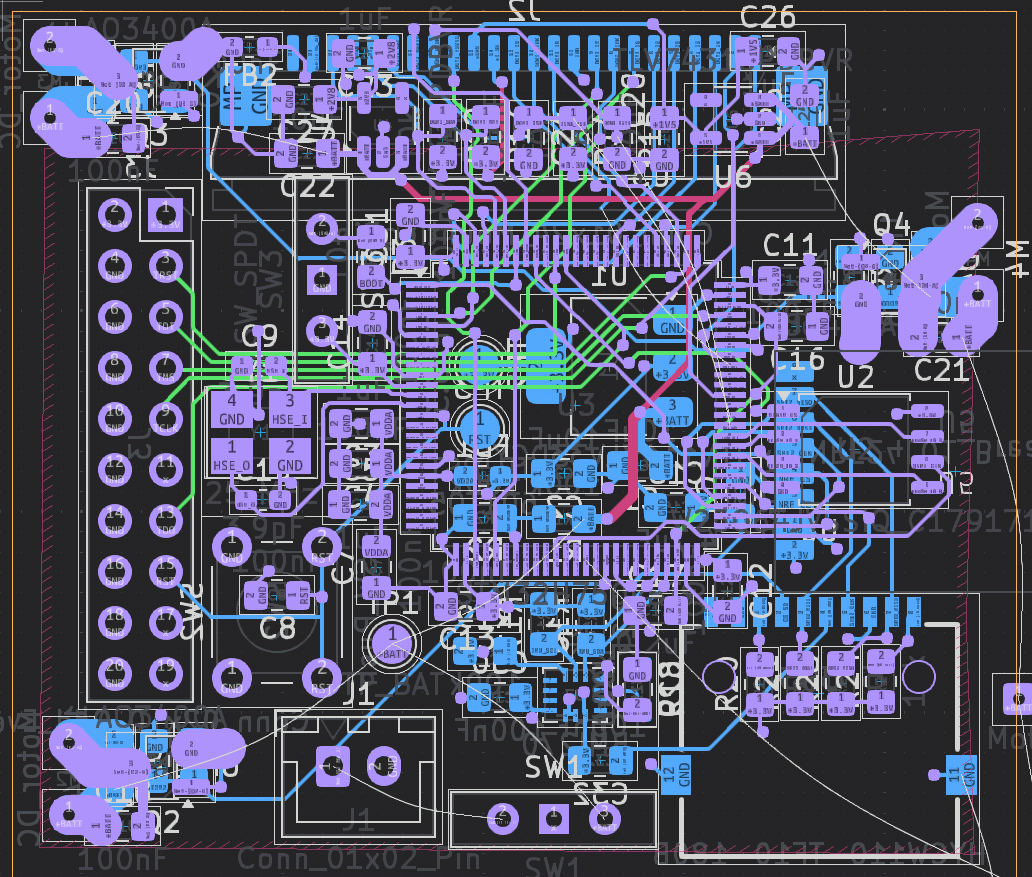
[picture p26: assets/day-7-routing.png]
Routing


Most of the routing is done, but we still need to do the last motor (figuring out where to place this will be hard) and a couple of the camera traces.

The last step will be to connect all of the battery nets. This is going to be pretty difficult as the tracks for the motors need to be really thick:

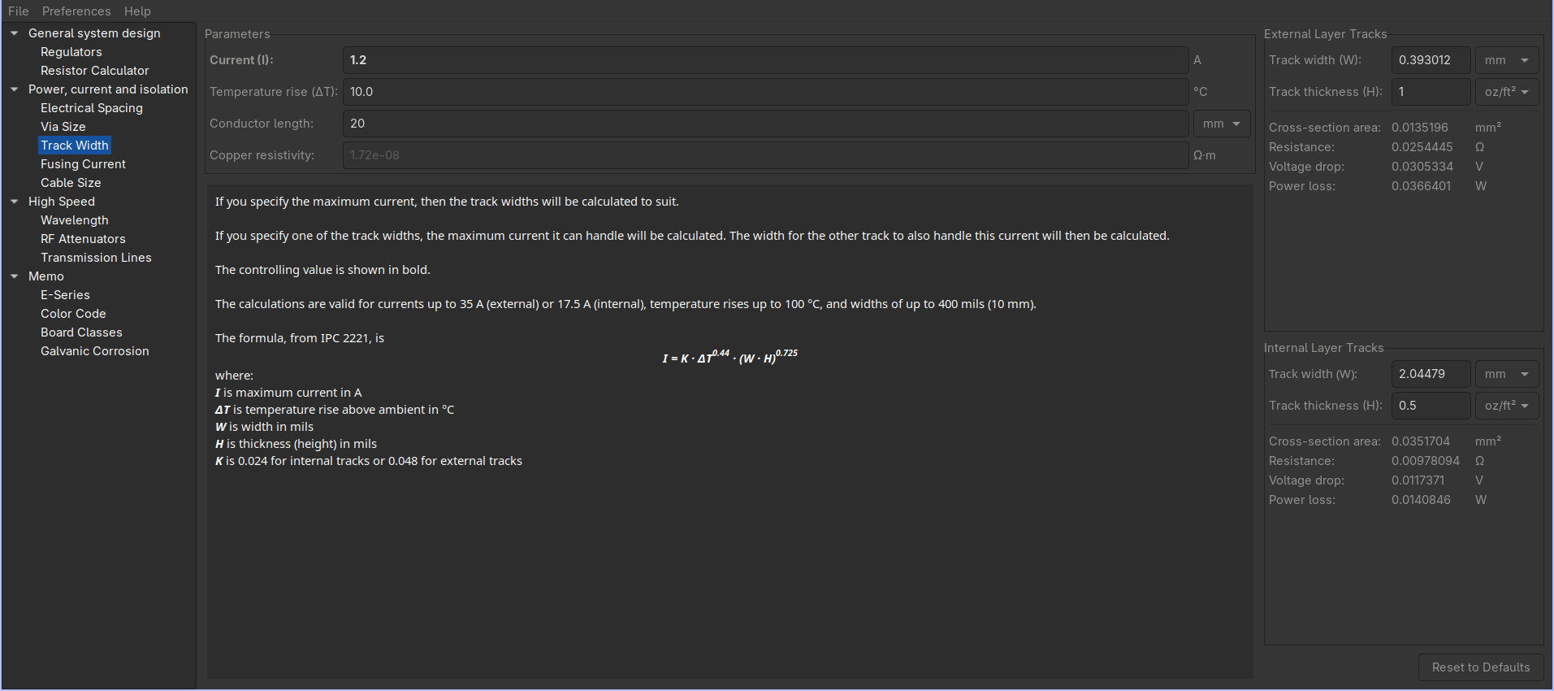
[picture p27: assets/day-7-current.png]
Track Width


Routing them on the external layers would require only a 0.4mm wide track, but there's not really much space left there.

The `In2.Cu` layer is _supposed_ to be for power, and this is where I'll probably end up routing them. The issue is that it's an internal layer, and the copper weight will be 0.5 oz/ft^2 (we could make it 1 oz, but we need to minimize weigh)

2 layer PCBs can be under 100x100mm before JLCPCB starts getting super expensive, but the cutoff is 50x50mm for 4 layers. Thankfully, we're just under that right now.

# July 1st-2nd

**Hours spent:**

Urjith: 2.5 (huddle)

Siddhant: 2.5 (huddle) + 2

We decided to lock in and actually finish the PCB.

The JTAG connector was taking up too much space, so Urjith invented the MONKE connector to solve this. (It's basically a rearranged JTAG connector without the duplicate GND/3.3V pins).

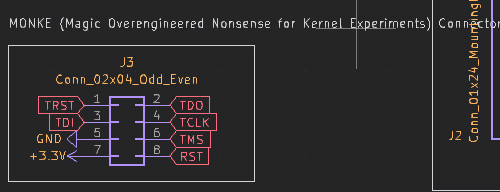
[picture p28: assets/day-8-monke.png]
MONKE


He also added a DUCKDUCKGOOSE connector for extensibility and to allow the development of potential HATs for the drone. To save pins, it can be configured to either expose the SPI or the I2C pins with a DPDT switch.

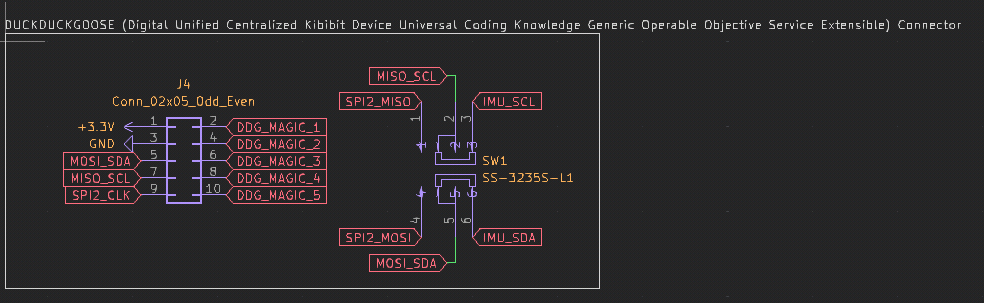
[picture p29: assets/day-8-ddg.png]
DDG


We also rearranged some of the MCU pins to make routing easier. We realized that using a dedicated 24Mhz crystal for the camera would be better than trying to use one of the MCU output crystals.

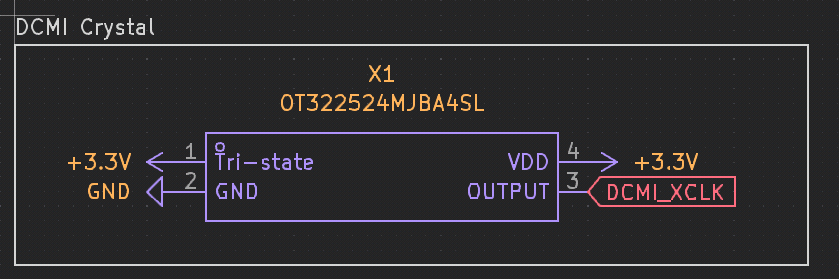
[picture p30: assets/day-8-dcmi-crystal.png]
crystal


Urjith replaced the boot switch with a solder jumper to save space.

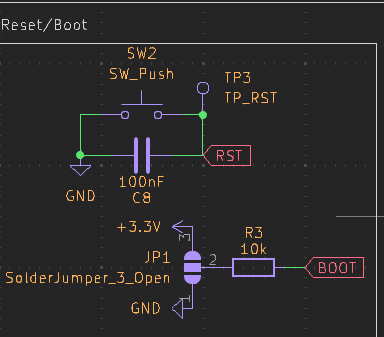
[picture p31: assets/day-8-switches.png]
switches


He then placed all the new components on the PCB.

After the huddle, Siddhant finished up the routing of the PCB. This involved moving the SD card and the NRF around to make routing easier.

The power traces were all routed on the external layers with 2mm tracks to ensure they would be able to provide enough current to the motors.

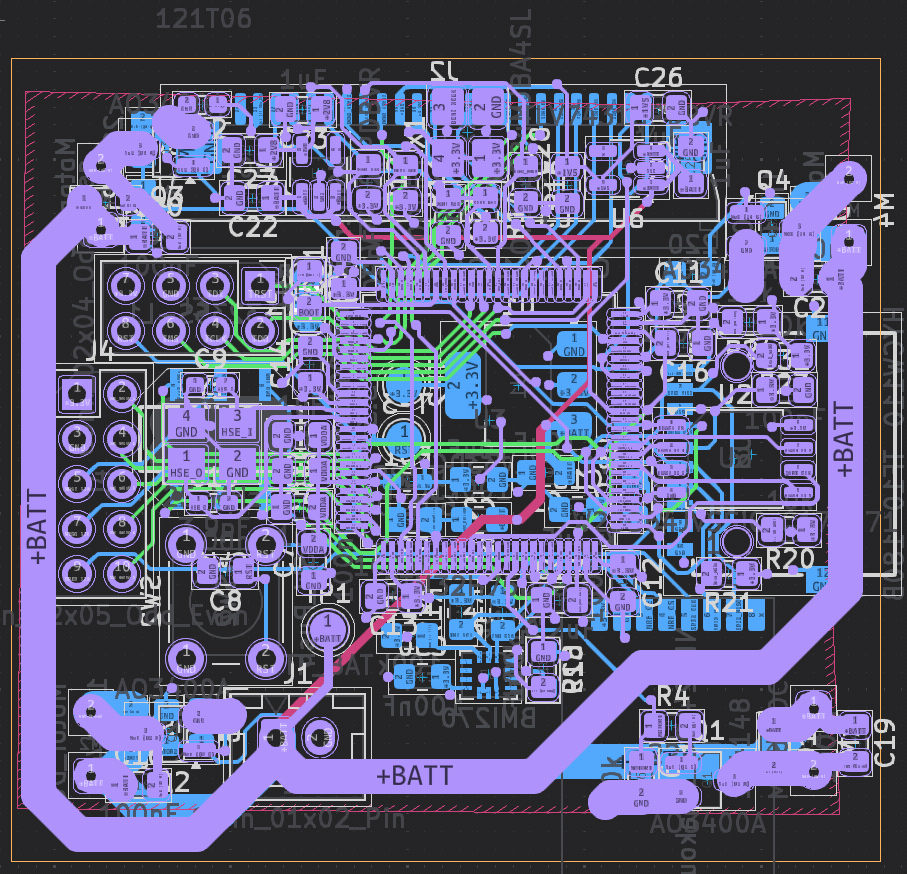
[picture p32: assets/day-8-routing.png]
pcb


# July 5th-9th

**Hours spent:**

Siddhant: 6

We realized that our current FPV system would be really slow - the nrf wouldn be able to cut it.

We decided to add FPV functionality on an extension board through our DDG connector.

I removed all the camera components and extended the DDG connector, both cleaning up a lot of the routing and minimizing the size of the PCB.

I added 5 extra GPIOs to the DDG connector and removed the I2C/SPI switch (and added dedicated pins)

To save space, I made the RST button SMD.

With the newly freed GPIO pins, I also added two extra buttons, some status LEDs, two neopixels, and a barometer.

I also added some silkscreen art. The PCB should hopefully be done!

### New Peripherals:

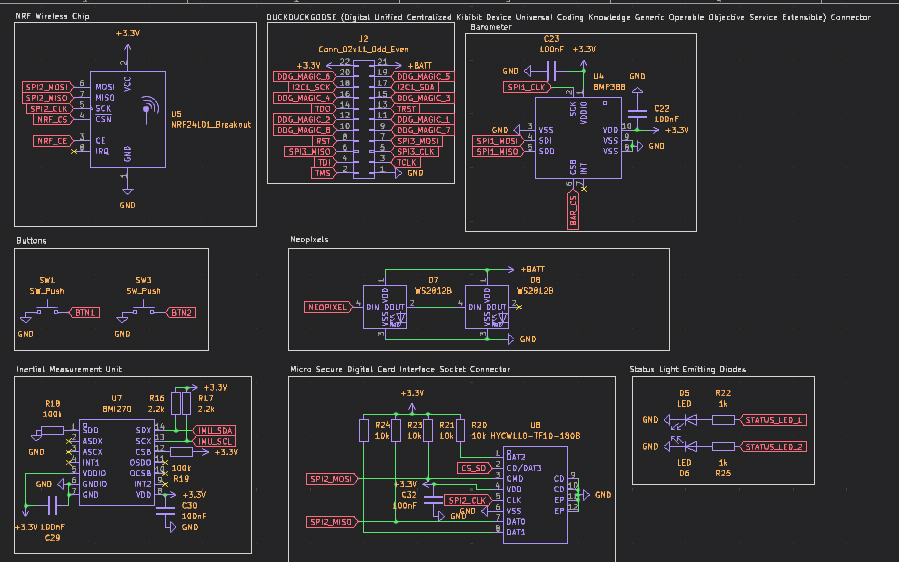
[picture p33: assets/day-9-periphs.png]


### Finished PCB (hopefully):

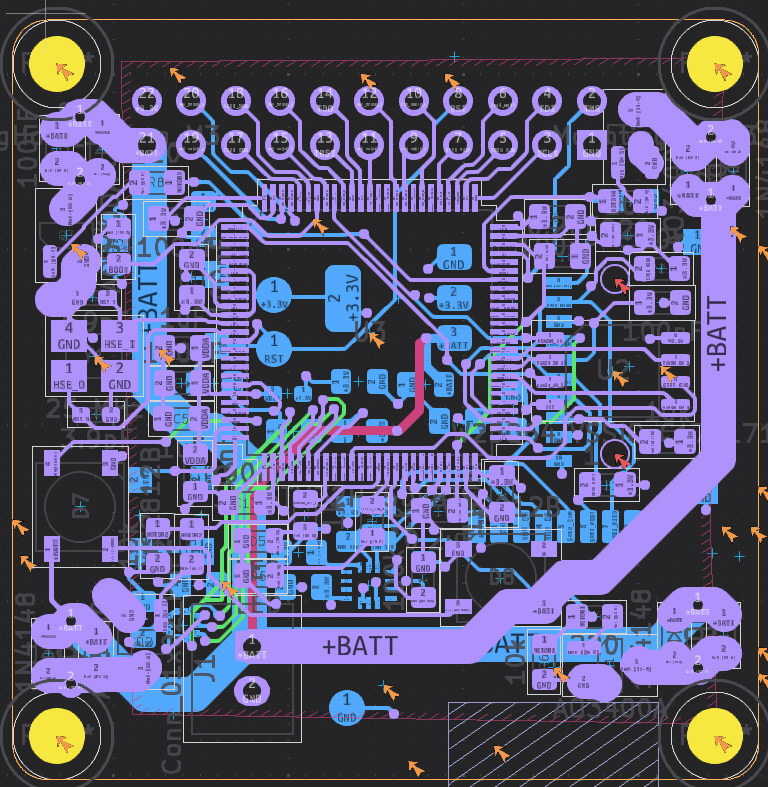
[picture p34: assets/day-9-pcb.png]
routing
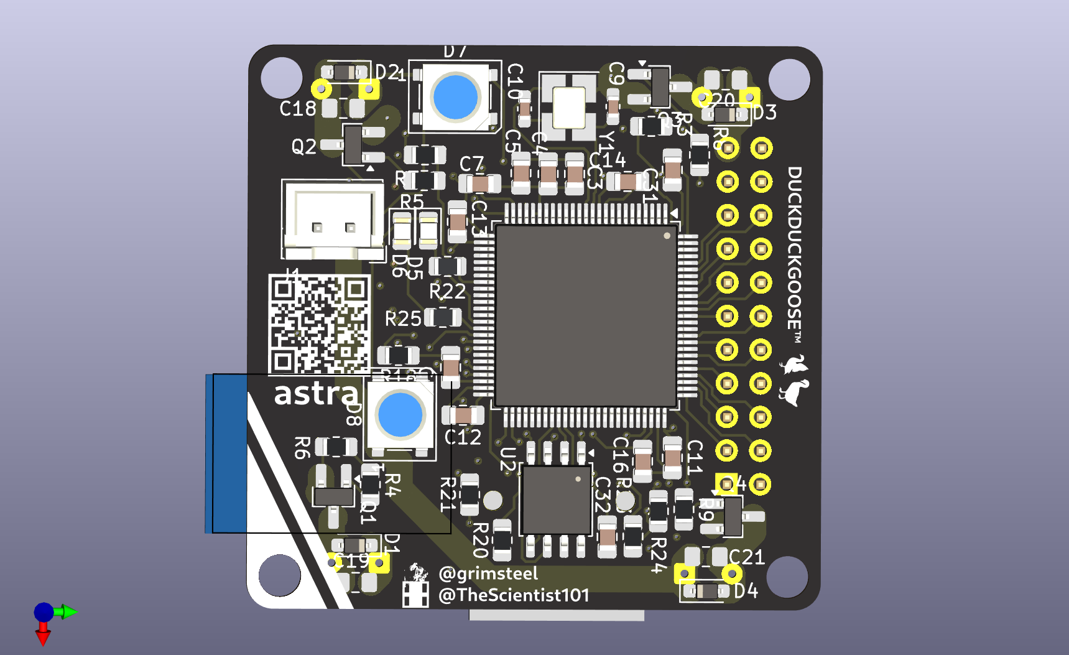
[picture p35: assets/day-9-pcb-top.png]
top
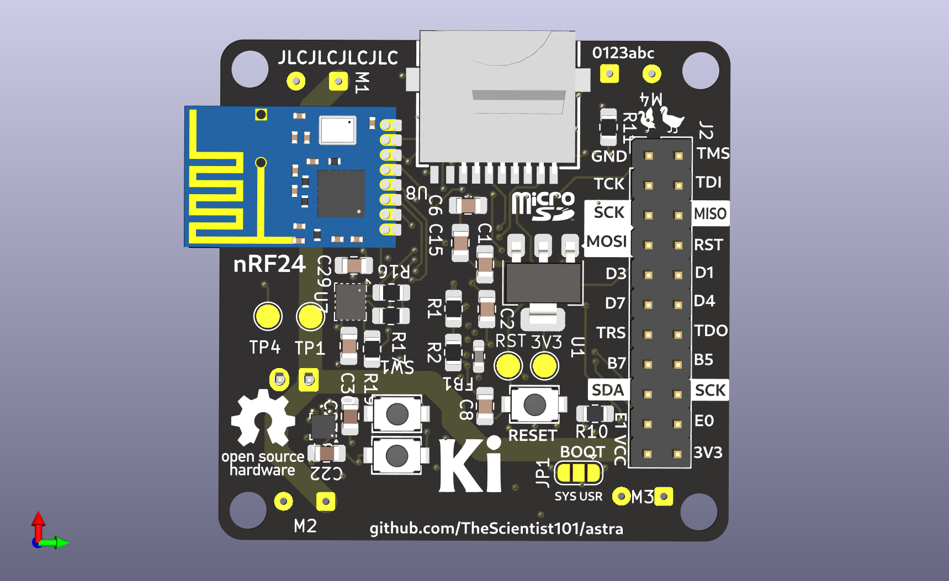
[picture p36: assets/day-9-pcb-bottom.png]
bottom
  

I also started work on the firmware. We're going to be using betaflight. The configuration is all done through a single config.h file.

# July 10th-14th

**Hours spent:**

Urjith: 2.5 (huddle) + 7 on controller

Siddhant: 2.5 (huddle) + 2 on controller + 3 on frame + 2 on firmware and pcb improvements

We designed the PCB for the controller. Apart from the devboard and NRF chip, it is a simple controller with two joysticks, 4 buttons, and three status leds. We initially wanted to use a Raspberry Pi Pico, but we decided to use an ESP32 C3 Supermini instead to save space on the PCB. Additionally, the ESP32 has built-in Wi-Fi which could allow us to pair a phone as an alternative controller.

While this should have been a simple PCB, we ran into trouble due to the devboard's lack of GPIOs. We initially thought to use a keyboard matrix: a technique we had learned from Hack Club's Hackpad program. While this would have allowed us to fit all of our components on the board, we were concerned about problems arising from integrating the joystick into the matrix. Since PCB iterations have become quite costly, we decided to use a simpler design that took advantage of a priority encoder. This allowed us to only use 3 GPIO pins for the 6 buttons (four actual buttons and two pressable joysticks). Finally, we also decided to use neopixels for our status LEDs, as they only require a single GPIO pin and can be controlled easily. However, we may decide switch to an SPI OLED since it can convey more information.

After Urjith designed most of the schematic, Siddhant did most of the PCB design.

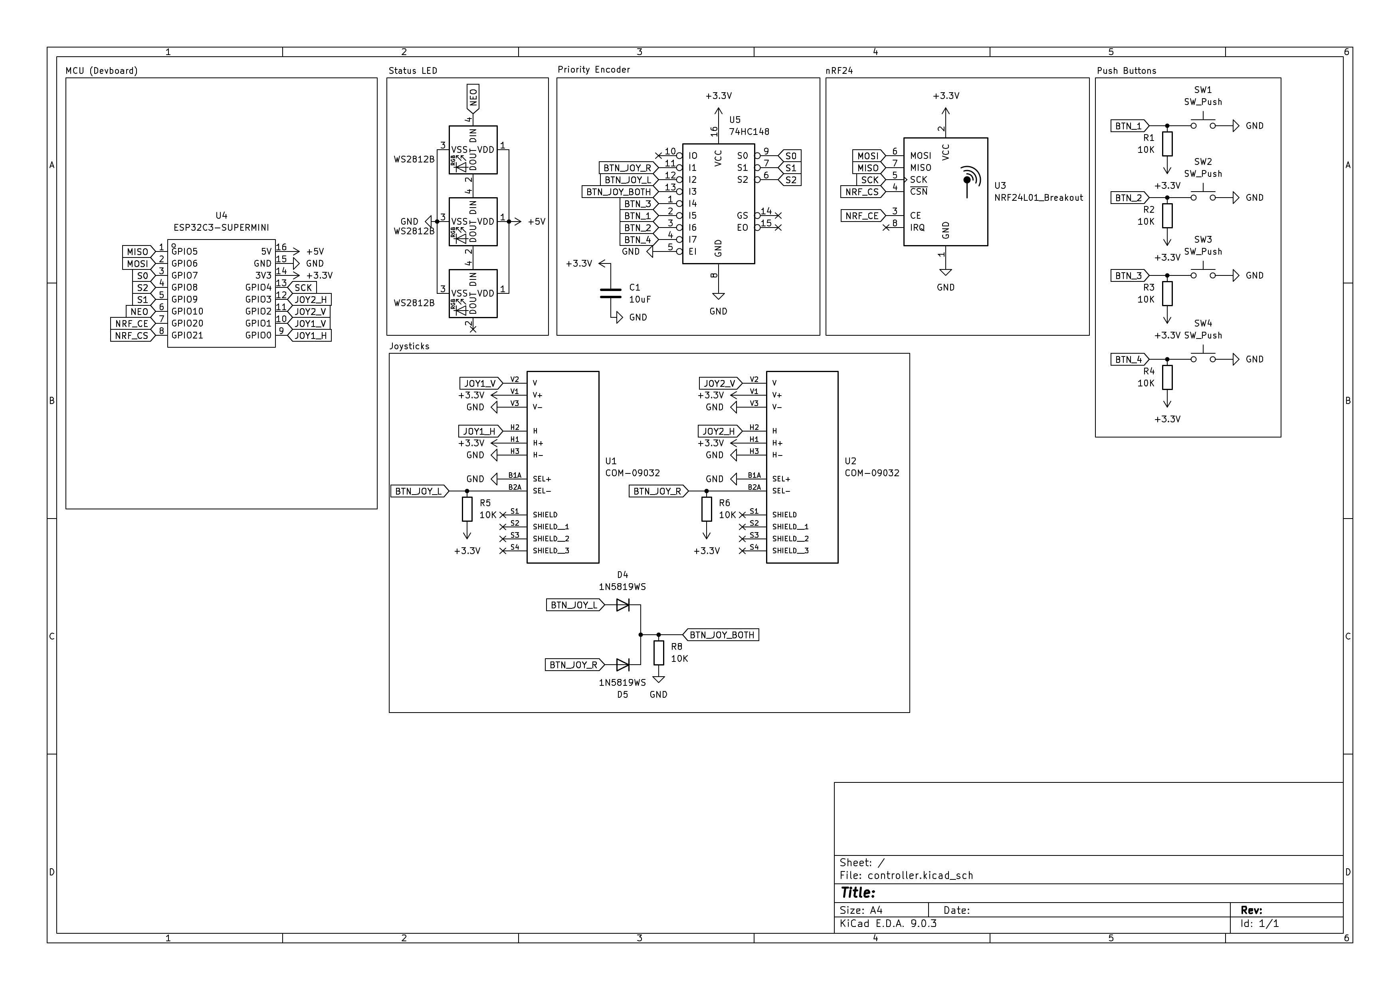
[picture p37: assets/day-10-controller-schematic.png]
Controller Schematic

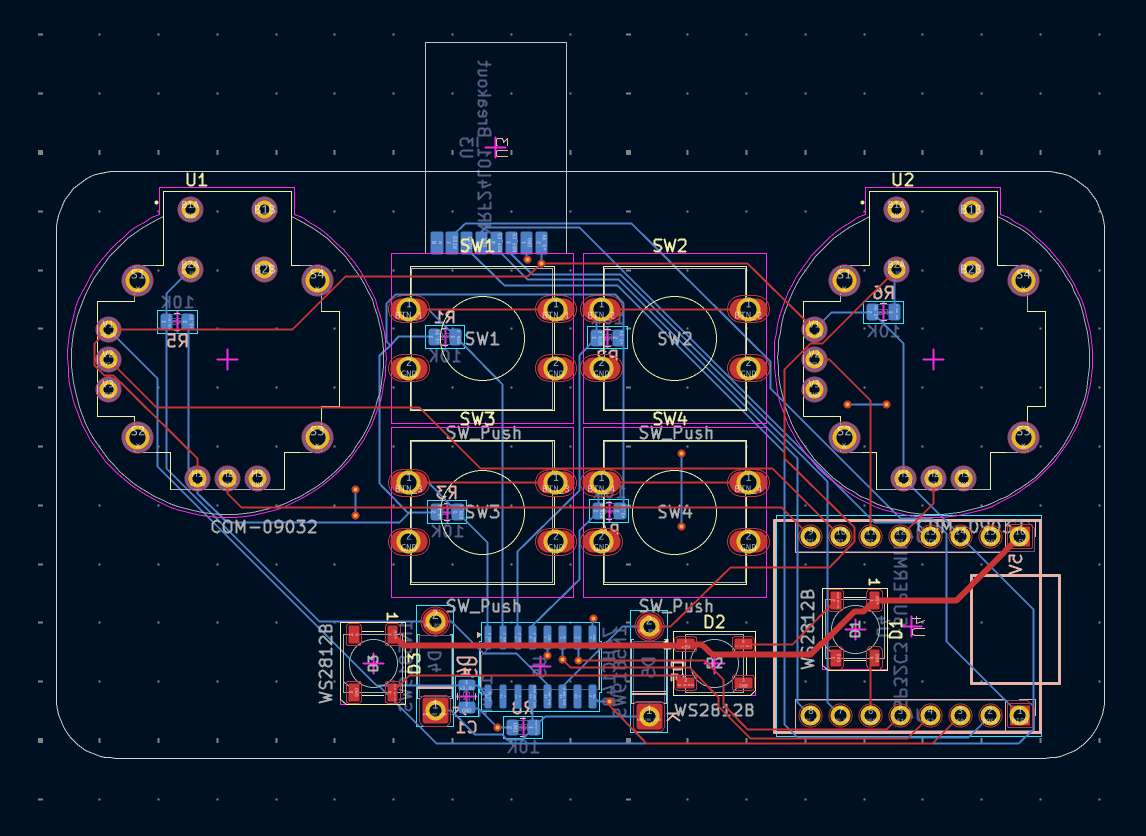
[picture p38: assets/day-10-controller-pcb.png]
Controller PCB


Siddhant also designed a case/frame for the drone in Onshape. It looks immaculate if I do say so myself. I plan to add a perching mechanism and some mounting hooks for DDG extensions.

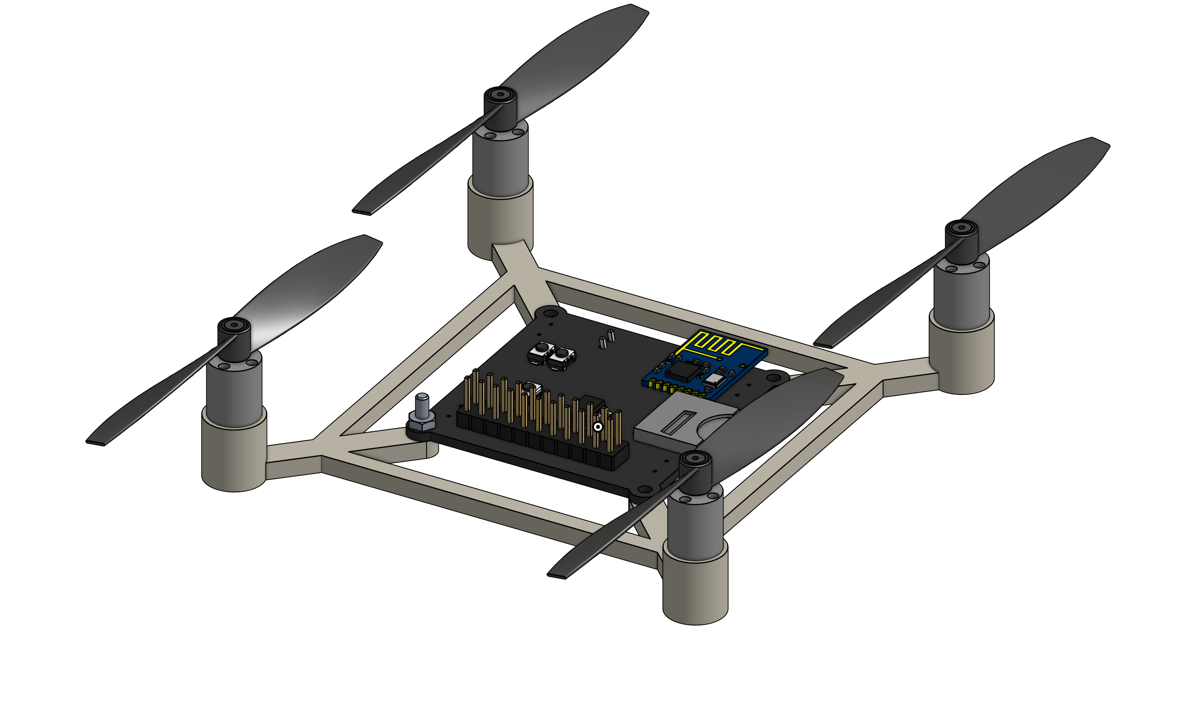
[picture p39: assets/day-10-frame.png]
Frame


He also finished the betaflight configuration, changed the IMU to use SPI, added SD card detection (to see if an SD card is actually in the holder) and added a barometer to the drone.

# July 15th

**Hours spent:**

Urjith: 1

I tested some if the pinout for some joysticks I have should work for the controller, and they should. It took a while since the pins of the joysticks weren't long enough for the jumper wires, and I had to hold them in place while testing. I used this simple micropython script on a pico to test.

```python
from machine import ADC,Pin
import time

axis = ADC(Pin(28, Pin.IN))

while True:
    axis = axis.read_u16() / 65535.0
    print(f"value:{axis}")
    time.sleep(0.1)
```

# July 17th-19th

**Hours spent:**

Siddhant: 5

I wrote the firmware for the transmitter/controller. It uses `esp-idf`, and we're using the V202 protocol for transmission between the transmitter and the drone.

Right now, the firmware is pretty basic. It has an ADC sampling loop for the joysticks and sends the latest joystick values to the drone every 50ms.

I ended up adding an external ADC for the joysticks instead of relying on the built in ESP32 ADC as we do need a higher level of accuracy.

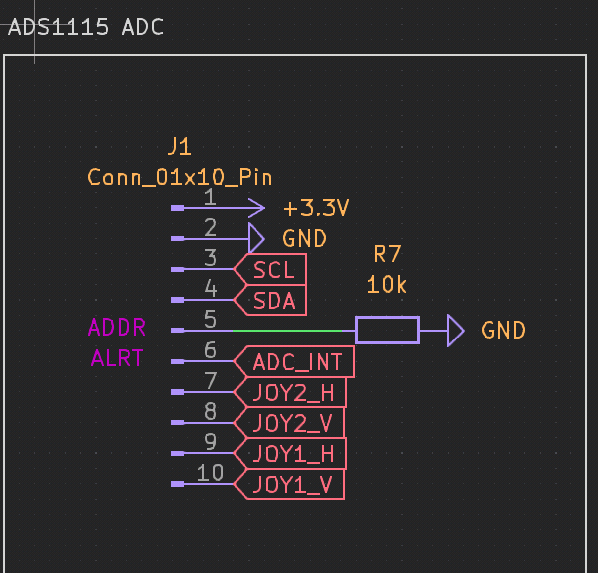
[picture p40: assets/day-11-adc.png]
adc


The ESP32 isn't very powerful, so in order to ensure that it's still responsive, I wrote this code to scale the raw ADC value into one between 0 and 255:

```cpp
/// Scale a signed 16-bit 3.3V ADC value to an unsigned byte
uint8_t scale_adc_value(int16_t value) {
  uint32_t unsigned_value = value < 0 ? 0 : value;
  // max input voltage: 3.3V
  // max range: 4.096V
  // max output value (theoretical): 2^15
  // max actual output value: 3.3V/4.096V * 2^15 = 26400
  // 26400 * 5 >> 9 = 257 (which is really close to 255)
  // 26214 * 5 >> 9 = 255 (max value that yields 255)
  uint8_t result = 255;
  if (unsigned_value <= 26214) {
    result = (unsigned_value * 5) >> 9;
  }
  return result;
}
```

# July 20th

**Hours spent:**

Urjith: 6

Siddhant: 3

I spent some time polishing up the overall project. I added a battery holder to the frame, and exported the production files for the CAD and PCB to the repo.

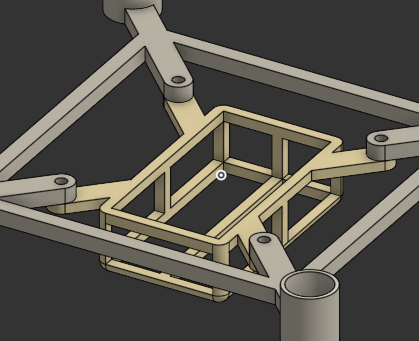
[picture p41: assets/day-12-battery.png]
battery holder


I ended up switching out our battery for a lighter one, even though it has a lower capacity. Even though this will result in a reduced flight time, it should still be in the 3-4 minute range.

I'm actually not 100% sure what battery connector this uses, so I asked in #electronics to see if anyone recognizes it. If all else fails, we can solder our own connector on fairly easily.

I also added an FPV connector to the PCB, as this will be cheaper than making a DDG extension board. We should be able to directly plug in the FPV module we're buying into the PCB through this.

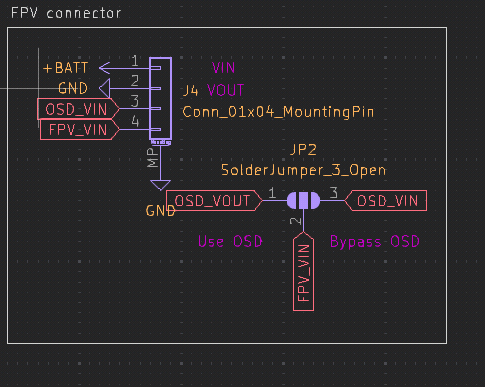
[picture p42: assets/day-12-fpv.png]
fpv


Routing this was pretty hard, as space is scarce in the PCB, but I was able to do it pretty easily on In1.Cu after I moved the IMU to get some more space.

It's me Urjith from here on out in today's journal entry (before it was Siddhant).

I designed the case for the controller. I thought it would be cool to sandwich the PCB between two parts of a case since it would look pretty bare-bones. I designed the case in OpenSCAD, and it took a while to get the dimensions right, but I think it looks pretty good.

While designing the case for the controller, I double-checked the joystick footprint and realized that the footprint I had was wrong. I had to change the footprint in the PCB, which was a bit of a pain, but luckily I didn't have to reroute too much. Subsequently I had to adjust the case to fit the new footprint, but that was pretty easy.

I also had to add M2 holes to the PCB for the case screws. I am realizing as I am typing this that both of the holes are near the front, which might be problematic. I should probably add some more holes to the back of the PCB.

Designing the case took a while because converting the coordinates from the PCB to OpenSCAD was a little tedious. Luckily, I got most of the coordinates right on my first try, so I didn't have to redo the case too much (except for the joysticks).

Gosh that took longer than I expected. I used to like OpenSCAD, but now I am not so sure.

controller case

Checking back in, I added an additional mounting hole so that the PCB is more secure in the case. This should be the final version of the case. (I also changed OpenSCAD to dark mode, which is why the colors are different)

controller case final

# July 21st

**Hours spent:**

Urjith: 1
Siddhant: 1

We're polishing up the project for submission.

I updated the README to include pictures of the controller and added a "why" section to explain why we made this drone.

Siddhant has been working on the finalizing the BOM and is adding silkscreen art to the controller PCB.

This is definitely not our last entry as we will document the assembly and testing of the drone.

I also want to make an extension board for the drone... I'm not exactly sure what it will do but we need to test the DUCKDUCKGOOSE connector.

Maybe GPS?

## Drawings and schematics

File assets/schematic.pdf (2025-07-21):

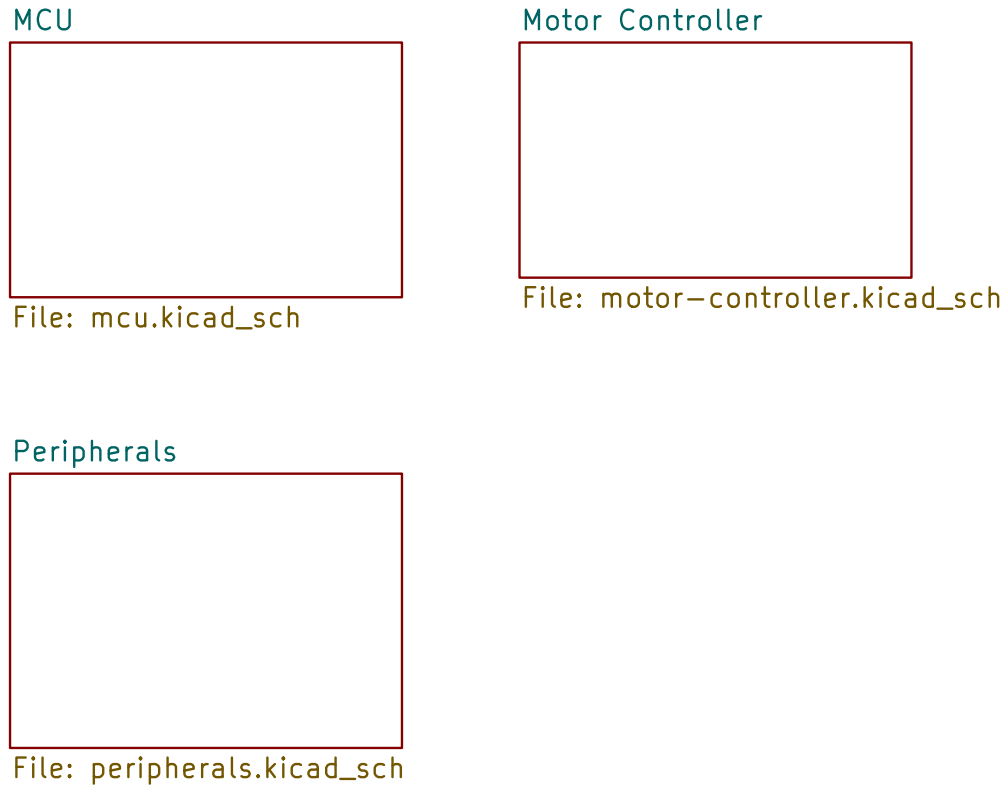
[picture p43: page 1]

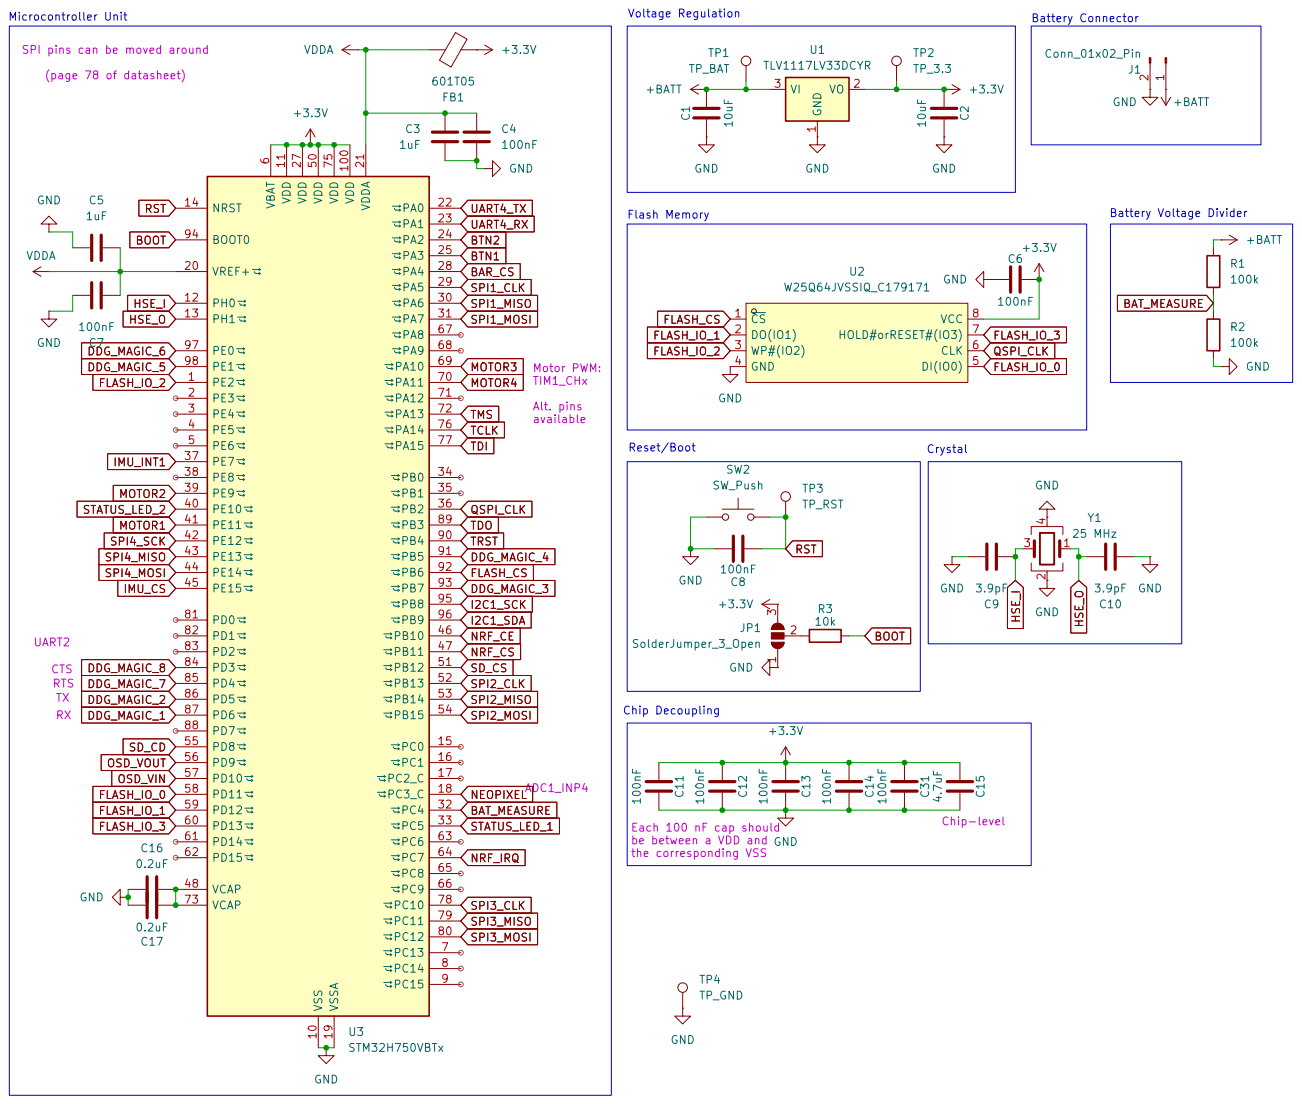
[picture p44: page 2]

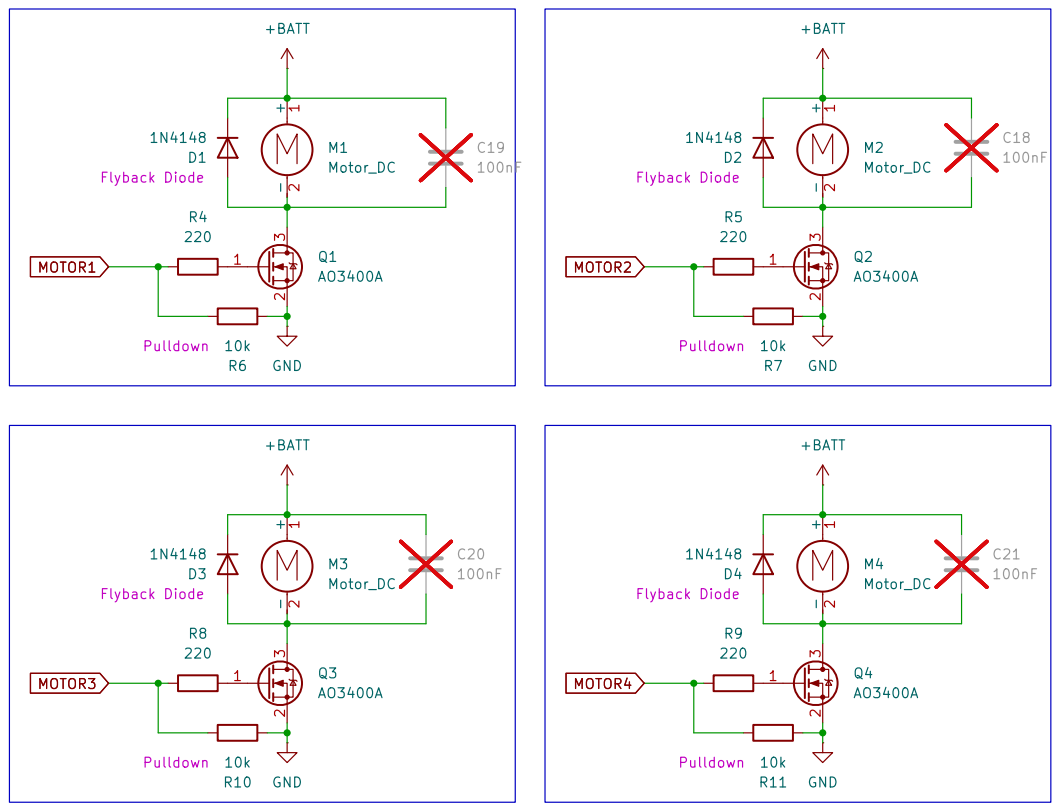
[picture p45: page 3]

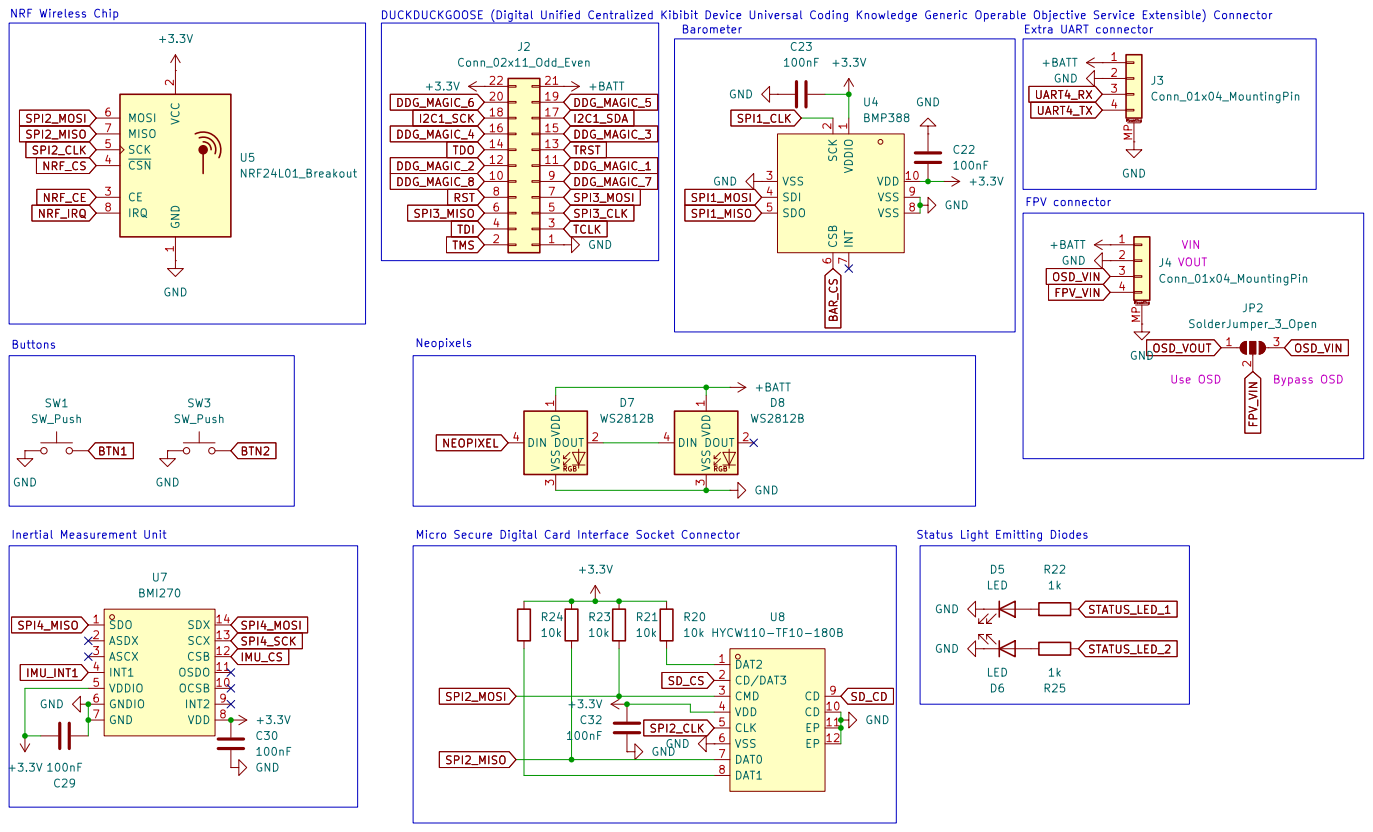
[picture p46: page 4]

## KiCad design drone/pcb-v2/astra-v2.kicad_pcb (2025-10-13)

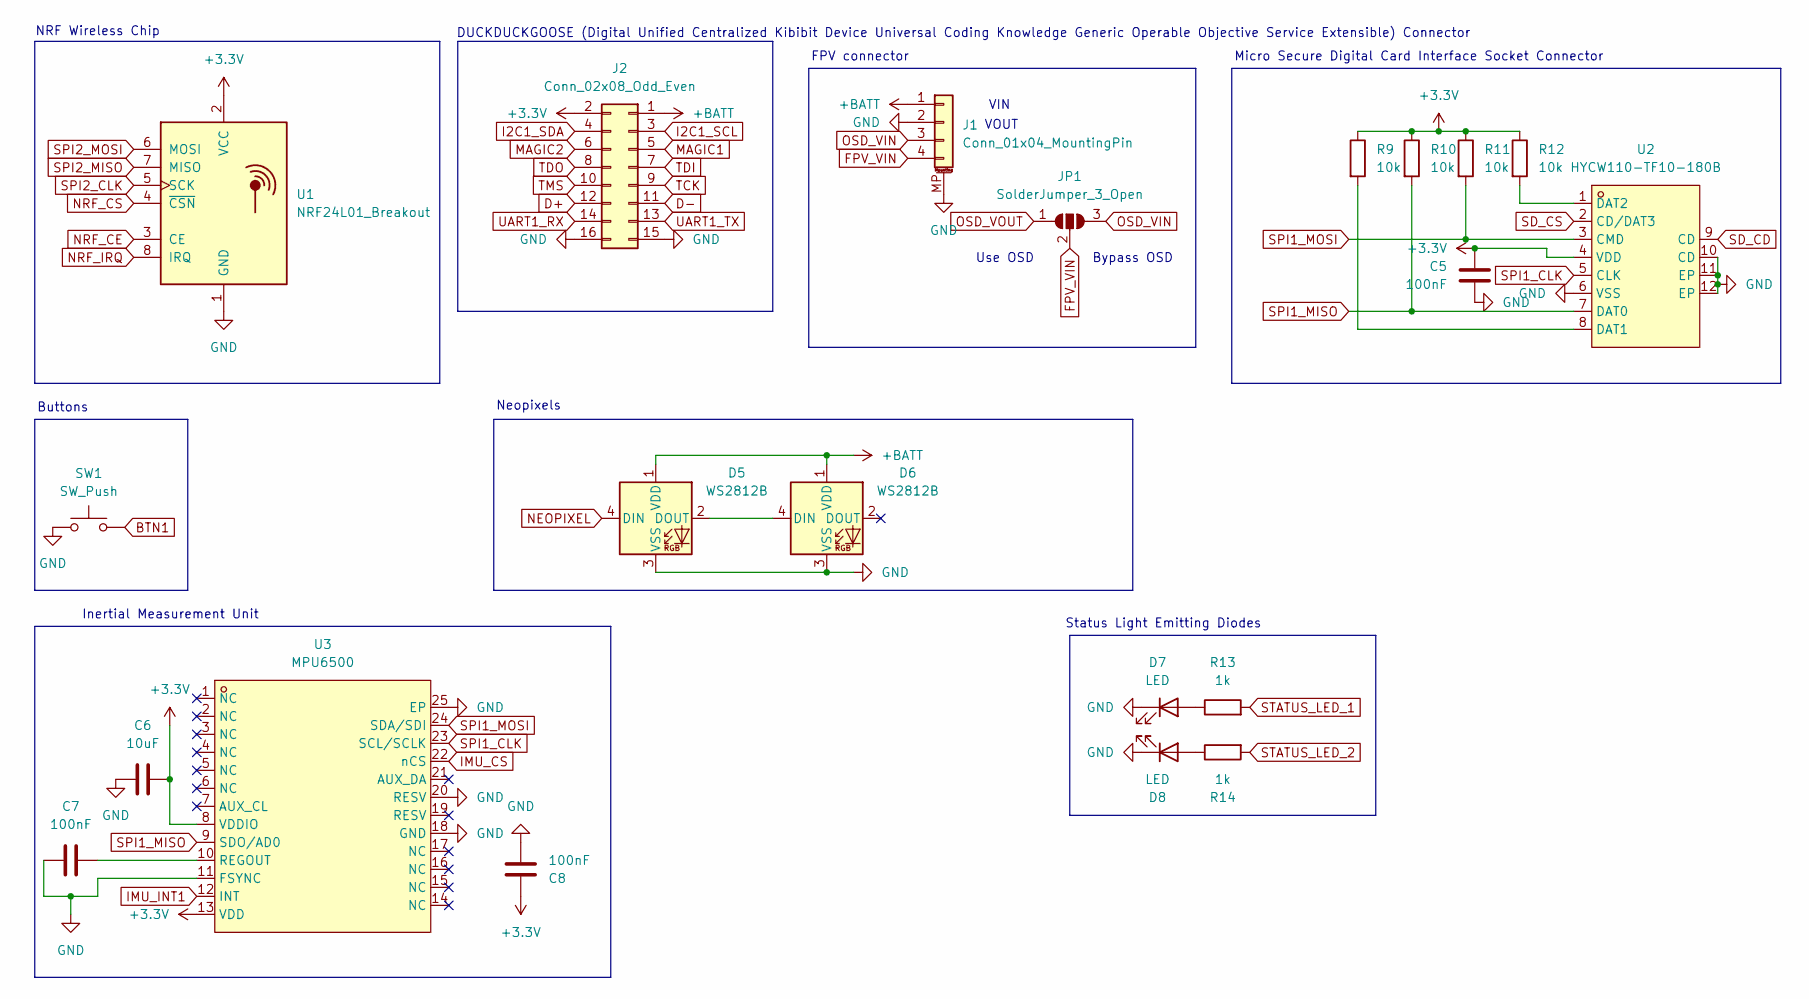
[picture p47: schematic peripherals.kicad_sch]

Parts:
C5: 100nF; C_0805_2012Metric_Pad1.18x1.45mm_HandSolder
C6: 10uF; C_0603_1608Metric
C7, C8: 100nF; C_0603_1608Metric; LCSC C14663
D5, D6: WS2812B; LED_WS2812B_PLCC4_5.0x5.0mm_P3.2mm
D7, D8: LED; LED_0805_2012Metric
J1: Conn_01x04_MountingPin; JST_SH_BM04B-SRSS-TB_1x04-1MP_P1.00mm_Vertical
J2: Conn_02x08_Odd_Even; PinHeader_2x08_P2.54mm_Vertical
JP1: SolderJumper_3_Open; SolderJumper-3_P1.3mm_Open_RoundedPad1.0x1.5mm
R9, R10, R11, R12: 10k; R_0805_2012Metric; LCSC C17414
R13, R14: 1k; R_0805_2012Metric_Pad1.20x1.40mm_HandSolder
SW1: SW_Push; SW-SMD_L4.0-W2.9-LS5.0
U1: NRF24L01_Breakout; nRF24L01_SMD_Breakout
U2: HYCW110-TF10-180B; SIM-SMD_HYCW110-TF10-180B; LCSC Part C2962030
U3: MPU6500; QFN-24-1EP_3x3mm_P0.4mm_EP1.75x1.6mm; LCSC C50278

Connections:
+3.3V: C5.1, C6.2, C8.1, J2.2, R9.1, R10.1, R11.1, R12.1, U1.2 (VCC), U2.4 (VDD), U3.8 (VDDIO), U3.13 (VDD); also elsewhere on the board
+BATT: D5.1 (VDD), D6.1 (VDD), J1.1, J2.1; also elsewhere on the board
BTN1: SW1.2; also elsewhere on the board
D+: J2.12; also elsewhere on the board
D-: J2.11; also elsewhere on the board
FPV_VIN: J1.4, JP1.2 (C)
GND: C5.2, C6.1, C7.2, C8.2, D5.3 (VSS), D6.3 (VSS), D7.1 (K), D8.1 (K), J1.2, J1.MP (MountPin), J2.15, J2.16, SW1.1, U1.1 (GND), U2.6 (VSS), U2.10 (CD), U2.11 (EP), U2.12 (EP), U3.11 (FSYNC), U3.18 (GND), U3.20 (RESV), U3.25 (EP); also elsewhere on the board
I2C1_SCL: J2.3; also elsewhere on the board
I2C1_SDA: J2.4; also elsewhere on the board
IMU_CS: U3.22 (nCS); also elsewhere on the board
IMU_INT1: U3.12 (INT); also elsewhere on the board
MAGIC1: J2.5; also elsewhere on the board
MAGIC2: J2.6; also elsewhere on the board
NEOPIXEL: D5.4 (DIN); also elsewhere on the board
NRF_CE: U1.3 (CE); also elsewhere on the board
NRF_CS: U1.4 (~CSN); also elsewhere on the board
NRF_IRQ: U1.8 (IRQ); also elsewhere on the board
unnamed: D5.2 (DOUT), D6.4 (DIN)
unnamed: D7.2 (A), R13.1
unnamed: D8.2 (A), R14.1
unnamed: R9.2, U2.8 (DAT1)
unnamed: R12.2, U2.1 (DAT2)
unnamed: C7.1, U3.10 (REGOUT)
OSD_VIN: J1.3, JP1.3 (B)
OSD_VOUT: JP1.1 (A)
SD_CD: U2.9 (CD); also elsewhere on the board
SD_CS: U2.2 (CD/DAT3); also elsewhere on the board
SPI1_CLK: U2.5 (CLK), U3.23 (SCL/SCLK); also elsewhere on the board
SPI1_MISO: R10.2, U2.7 (DAT0), U3.9 (SDO/AD0); also elsewhere on the board
SPI1_MOSI: R11.2, U2.3 (CMD), U3.24 (SDA/SDI); also elsewhere on the board
SPI2_CLK: U1.5 (SCK); also elsewhere on the board
SPI2_MISO: U1.7 (MISO); also elsewhere on the board
SPI2_MOSI: U1.6 (MOSI); also elsewhere on the board
STATUS_LED_1: R13.2; also elsewhere on the board
STATUS_LED_2: R14.2; also elsewhere on the board
TCK: J2.9; also elsewhere on the board
TDI: J2.7; also elsewhere on the board
TDO: J2.8; also elsewhere on the board
TMS: J2.10; also elsewhere on the board
UART1_RX: J2.14; also elsewhere on the board
UART1_TX: J2.13; also elsewhere on the board

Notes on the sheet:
Buttons
FPV connector
Neopixels
DUCKDUCKGOOSE (Digital Unified Centralized Kibibit Device Universal Coding Knowledge Generic Operable Objective Service Extensible) Connector
Use OSD
NRF Wireless Chip
Status Light Emitting Diodes
VOUT
Bypass OSD
Micro Secure Digital Card Interface Socket Connector
Inertial Measurement Unit
VIN

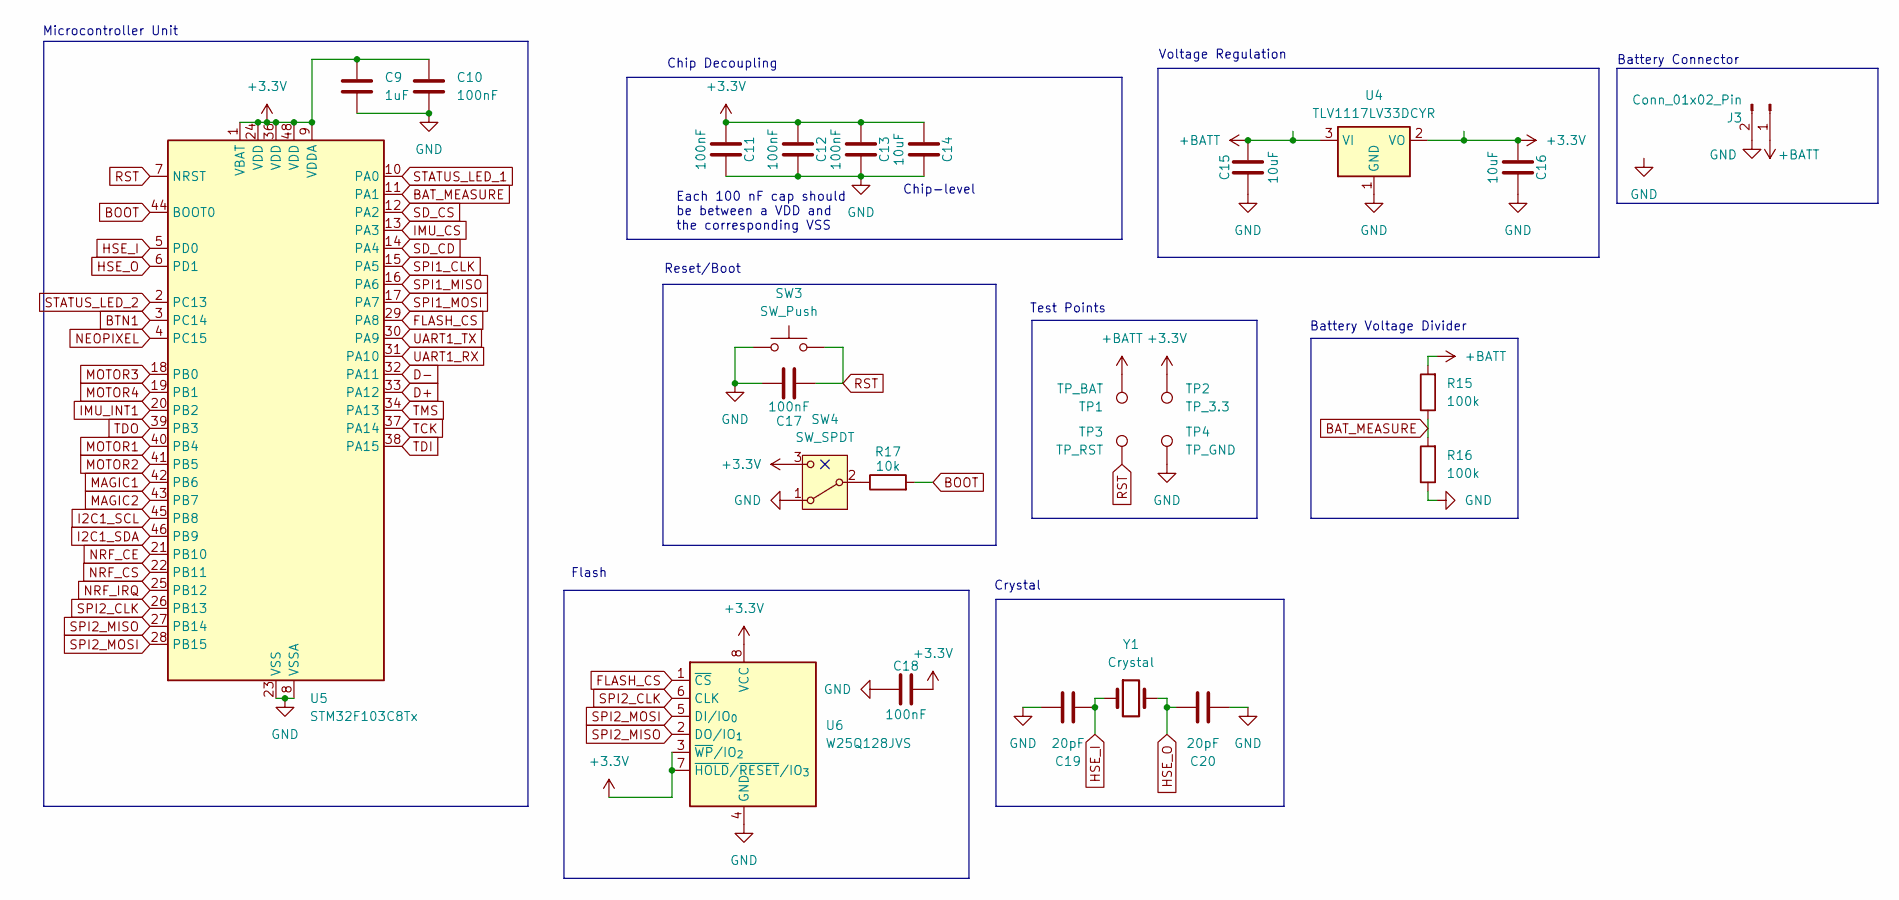
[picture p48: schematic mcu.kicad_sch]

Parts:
C9: 1uF; C_0603_1608Metric; LCSC C15849
C10, C11, C12, C13, C18: 100nF; C_0603_1608Metric; LCSC C14663
C14: 10uF; C_0603_1608Metric; LCSC C19702
C15, C16: 10uF; C_0805_2012Metric_Pad1.18x1.45mm_HandSolder
C17: 100nF; C_0805_2012Metric_Pad1.18x1.45mm_HandSolder
C19, C20: 20pF; C_0603_1608Metric; LCSC C1648
J3: Conn_01x02_Pin; SolderWire-0.1sqmm_1x02_P3.6mm_D0.4mm_OD1mm
R15, R16: 100k; R_0603_1608Metric; LCSC C25803
R17: 10k; R_0805_2012Metric; LCSC C17414
SW3: SW_Push; SW-SMD_L4.0-W2.9-LS5.0
SW4: SW_SPDT; SW_Slide-03_Wuerth-WS-SLTV_10x2.5x6.4_P2.54mm
TP1: TP_BAT; TestPoint_Pad_D2.0mm
TP2: TP_3.3; TestPoint_Pad_D2.0mm
TP3: TP_RST; TestPoint_Pad_D2.0mm
TP4: TP_GND; TestPoint_Pad_D2.0mm
U4: TLV1117LV33DCYR; SOT-223-3_TabPin2
U5: STM32F103C8Tx; LQFP-48_7x7mm_P0.5mm; LCSC C8734
U6: W25Q128JVS; SOIC-8_5.3x5.3mm_P1.27mm; LCSC C97521
Y1: Crystal; Crystal_SMD_5032-2Pin_5.0x3.2mm; LCSC C115962

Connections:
+3.3V: C9.1, C10.1, C11.1, C12.1, C13.1, C14.1, C16.1, C18.2, SW4.3 (C), TP2.1, U4.2 (VO), U5.1 (VBAT), U5.9 (VDDA), U5.24 (VDD), U5.36 (VDD), U5.48 (VDD), U6.3 (~WP/IO_{2}), U6.7 (~HOLD/~RESET/IO_{3}), U6.8 (VCC); also elsewhere on the board
+BATT: C15.2, J3.1, R15.2, TP1.1, U4.3 (VI); also elsewhere on the board
BAT_MEASURE: R15.1, R16.2, U5.11 (PA1)
BOOT: R17.2, U5.44 (BOOT0)
BTN1: U5.3 (PC14); also elsewhere on the board
D+: U5.33 (PA12); also elsewhere on the board
D-: U5.32 (PA11); also elsewhere on the board
FLASH_CS: U5.29 (PA8), U6.1 (~CS)
GND: C9.2, C10.2, C11.2, C12.2, C13.2, C14.2, C15.1, C16.2, C17.2, C18.1, C19.1, C20.2, J3.2, R16.1, SW3.1, SW4.1 (A), TP4.1, U4.1 (GND), U5.8 (VSSA), U5.23 (VSS), U5.35 (VSS), U5.47 (VSS), U6.4 (GND); also elsewhere on the board
HSE_I: C19.2, U5.5 (PD0), Y1.1
HSE_O: C20.1, U5.6 (PD1), Y1.2
I2C1_SCL: U5.45 (PB8); also elsewhere on the board
I2C1_SDA: U5.46 (PB9); also elsewhere on the board
IMU_CS: U5.13 (PA3); also elsewhere on the board
IMU_INT1: U5.20 (PB2); also elsewhere on the board
MAGIC1: U5.42 (PB6); also elsewhere on the board
MAGIC2: U5.43 (PB7); also elsewhere on the board
MOTOR1: U5.40 (PB4); also elsewhere on the board
MOTOR2: U5.41 (PB5); also elsewhere on the board
MOTOR3: U5.18 (PB0); also elsewhere on the board
MOTOR4: U5.19 (PB1); also elsewhere on the board
NEOPIXEL: U5.4 (PC15); also elsewhere on the board
NRF_CE: U5.21 (PB10); also elsewhere on the board
NRF_CS: U5.22 (PB11); also elsewhere on the board
NRF_IRQ: U5.25 (PB12); also elsewhere on the board
unnamed: R17.1, SW4.2 (B)
RST: C17.1, SW3.2, TP3.1, U5.7 (NRST)
SD_CD: U5.14 (PA4); also elsewhere on the board
SD_CS: U5.12 (PA2); also elsewhere on the board
SPI1_CLK: U5.15 (PA5); also elsewhere on the board
SPI1_MISO: U5.16 (PA6); also elsewhere on the board
SPI1_MOSI: U5.17 (PA7); also elsewhere on the board
SPI2_CLK: U5.26 (PB13), U6.6 (CLK); also elsewhere on the board
SPI2_MISO: U5.27 (PB14), U6.2 (DO/IO_{1}); also elsewhere on the board
SPI2_MOSI: U5.28 (PB15), U6.5 (DI/IO_{0}); also elsewhere on the board
STATUS_LED_1: U5.10 (PA0); also elsewhere on the board
STATUS_LED_2: U5.2 (PC13); also elsewhere on the board
TCK: U5.37 (PA14); also elsewhere on the board
TDI: U5.38 (PA15); also elsewhere on the board
TDO: U5.39 (PB3); also elsewhere on the board
TMS: U5.34 (PA13); also elsewhere on the board
UART1_RX: U5.31 (PA10); also elsewhere on the board
UART1_TX: U5.30 (PA9); also elsewhere on the board

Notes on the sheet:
Microcontroller Unit
Flash
Each 100 nF cap should be between a VDD and the corresponding VSS
Battery Voltage Divider
Chip Decoupling
Crystal
Test Points
Chip-level
Battery Connector
Reset/Boot
Voltage Regulation

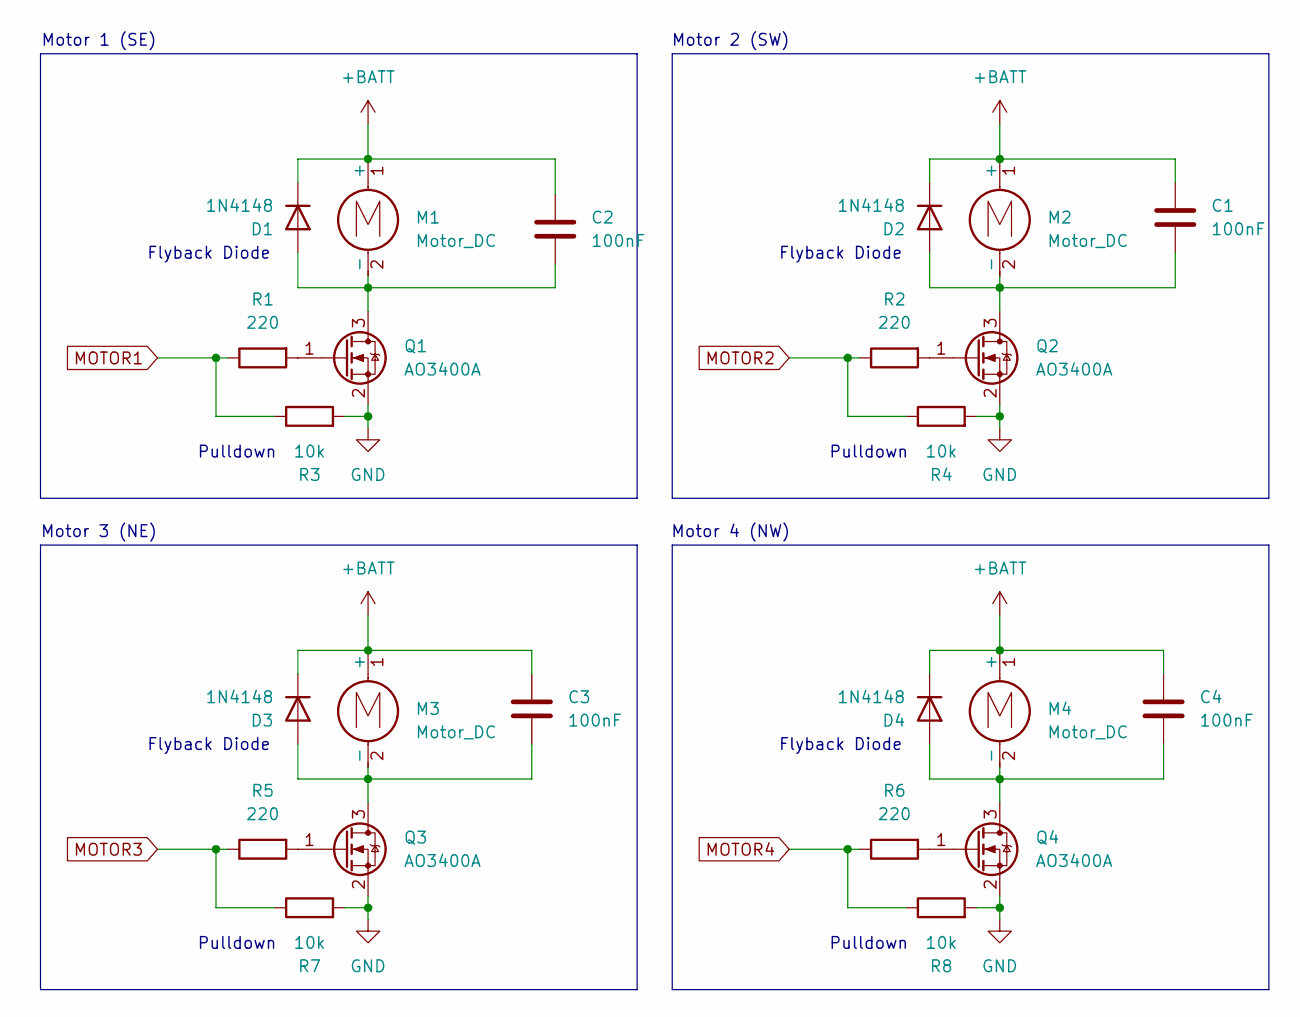
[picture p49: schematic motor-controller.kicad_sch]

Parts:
C1, C2, C3, C4: 100nF; C_0805_2012Metric_Pad1.18x1.45mm_HandSolder
D1, D2, D3, D4: 1N4148; D_SOD-323; LCSC C2128
M1, M2, M3, M4: Motor_DC; SolderWire-0.1sqmm_1x02_P3.6mm_D0.4mm_OD1mm
Q1, Q2, Q3, Q4: AO3400A; SOT-23-3; LCSC C20917
R1, R2, R5, R6: 220; R_0805_2012Metric; LCSC C17557
R3, R4, R7, R8: 10k; R_0805_2012Metric; LCSC C17414

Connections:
+BATT: C1.1, C2.1, C3.1, C4.1, D1.1 (K), D2.1 (K), D3.1 (K), D4.1 (K), M1.1 (+), M2.1 (+), M3.1 (+), M4.1 (+); also elsewhere on the board
GND: Q1.2 (S), Q2.2 (S), Q3.2 (S), Q4.2 (S), R3.2, R4.2, R7.2, R8.2; also elsewhere on the board
MOTOR1: R1.1, R3.1; also elsewhere on the board
MOTOR2: R2.1, R4.1; also elsewhere on the board
MOTOR3: R5.1, R7.1; also elsewhere on the board
MOTOR4: R6.1, R8.1; also elsewhere on the board
unnamed: C2.2, D1.2 (A), M1.2 (-), Q1.3 (D)
unnamed: C1.2, D2.2 (A), M2.2 (-), Q2.3 (D)
unnamed: C3.2, D3.2 (A), M3.2 (-), Q3.3 (D)
unnamed: C4.2, D4.2 (A), M4.2 (-), Q4.3 (D)
unnamed: Q1.1 (G), R1.2
unnamed: Q2.1 (G), R2.2
unnamed: Q3.1 (G), R5.2
unnamed: Q4.1 (G), R6.2

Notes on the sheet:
Pulldown
Motor 2 (SW)
Flyback Diode
Motor 1 (SE)
Motor 3 (NE)
Motor 4 (NW)

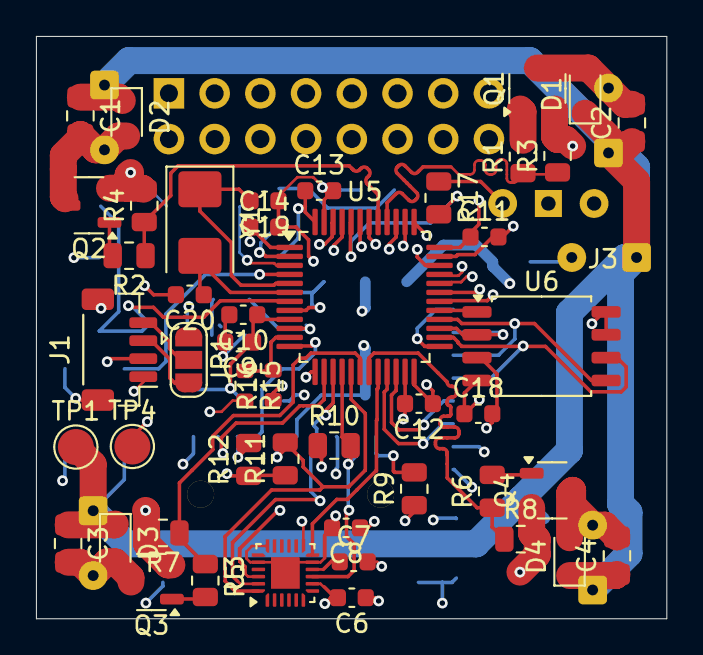
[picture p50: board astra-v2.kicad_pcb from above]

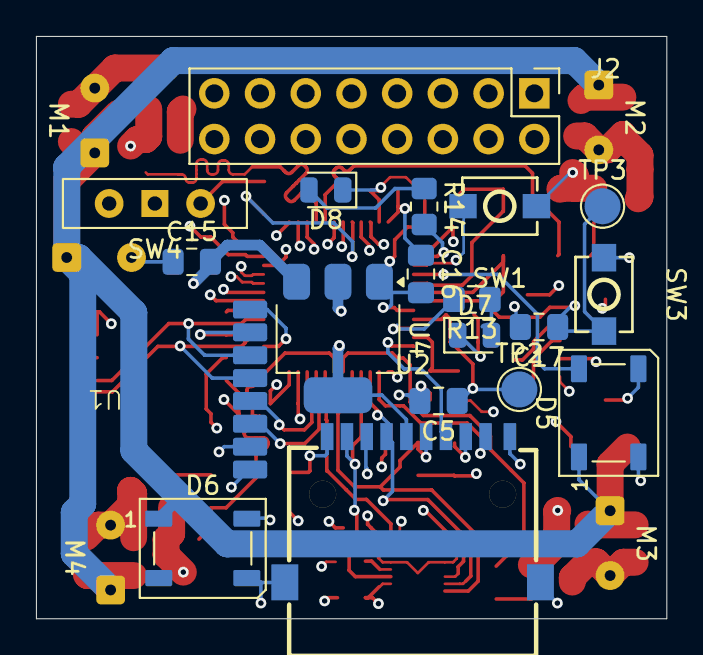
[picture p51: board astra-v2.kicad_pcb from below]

Board: 4 copper layers, 35.0 x 32.3 mm, 71 parts (23 on the bottom side), 59 nets.

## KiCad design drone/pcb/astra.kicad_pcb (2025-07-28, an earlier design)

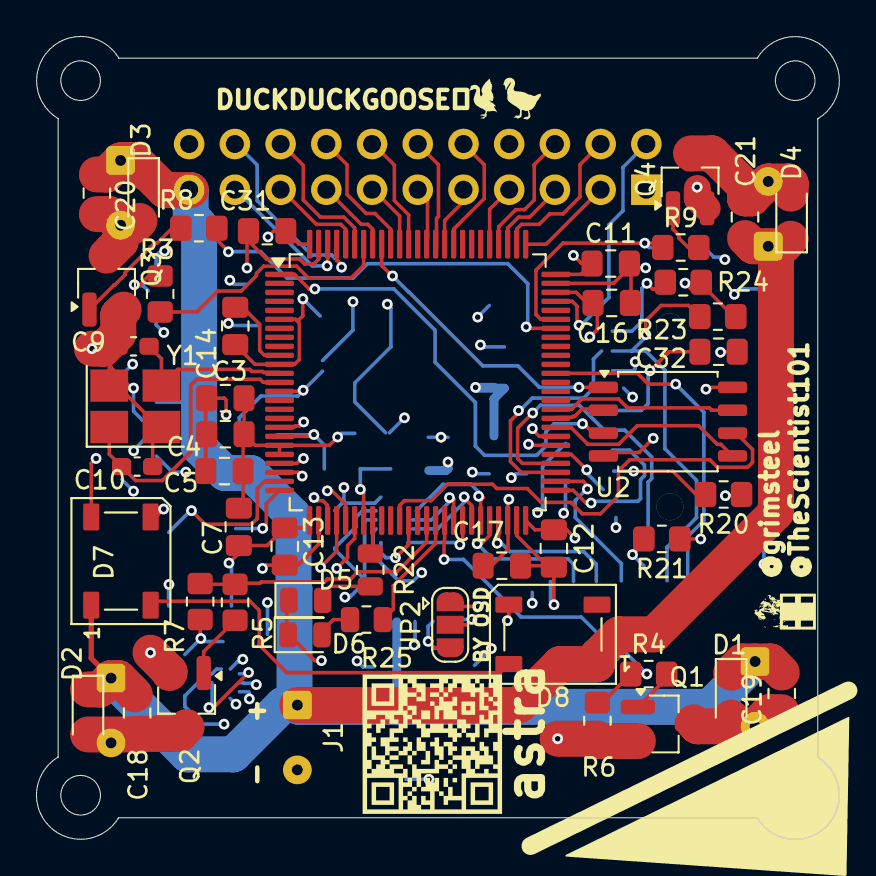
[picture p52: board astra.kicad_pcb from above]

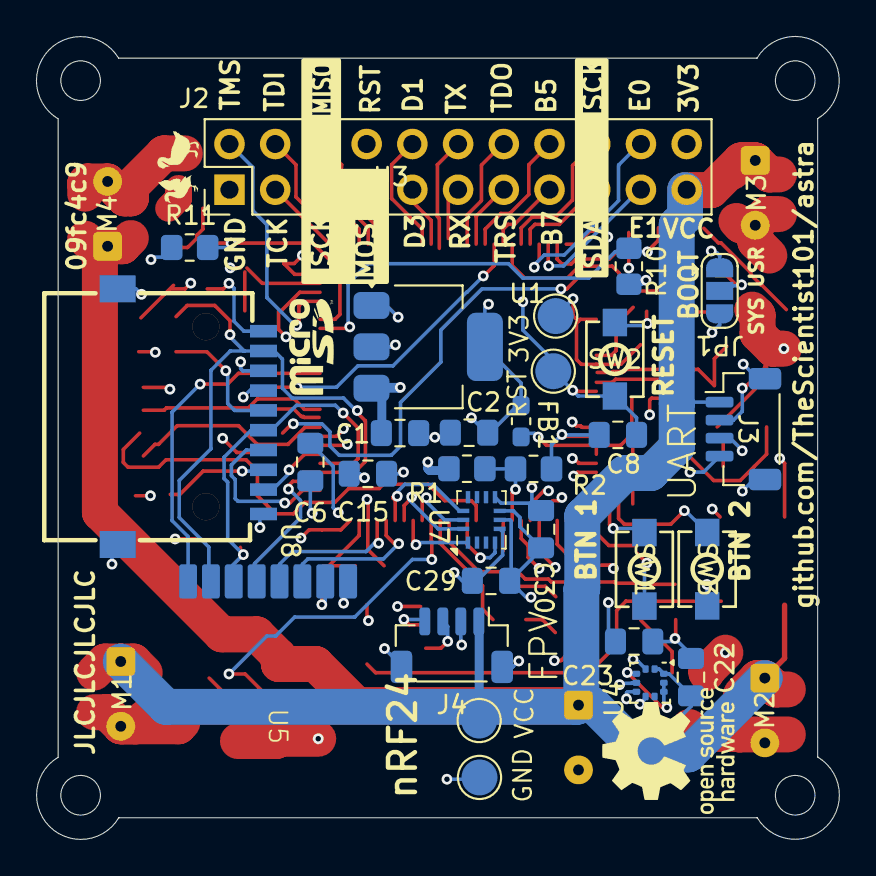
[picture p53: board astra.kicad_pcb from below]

Board: 4 copper layers, 44.6 x 44.6 mm, 83 parts (34 on the bottom side), 79 nets.

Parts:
C1, C2: 10uF; C_0805_2012Metric_Pad1.18x1.45mm_HandSolder
C3, C5: 1uF; C_0805_2012Metric_Pad1.18x1.45mm_HandSolder
C4, C6, C7, C8, C11, C12, C13, C14, C18, C19, C20, C21, C22, C23, C29, C30, C31, C32: 100nF; C_0805_2012Metric_Pad1.18x1.45mm_HandSolder
C9, C10: 3.9pF; C_0603_1608Metric_Pad1.08x0.95mm_HandSolder
C15: 4.7uF; C_0805_2012Metric_Pad1.18x1.45mm_HandSolder
C16, C17: 0.2uF; C_0805_2012Metric_Pad1.18x1.45mm_HandSolder
D1, D2, D3, D4: 1N4148; D_SOD-323_HandSoldering
D5, D6: LED; LED_0805_2012Metric
D7, D8: WS2812B; LED_WS2812B_PLCC4_5.0x5.0mm_P3.2mm
FB1: 601T05; L_0603_1608Metric_Pad1.05x0.95mm_HandSolder
J1: Conn_01x02_Pin; SolderWire-0.1sqmm_1x02_P3.6mm_D0.4mm_OD1mm
J2: Conn_02x11_Odd_Even; PinHeader_2x11_P2.54mm_Vertical
J3, J4: Conn_01x04_MountingPin; JST_SH_BM04B-SRSS-TB_1x04-1MP_P1.00mm_Vertical
JP1, JP2: SolderJumper_3_Open; SolderJumper-3_P1.3mm_Open_RoundedPad1.0x1.5mm
M1, M2, M3, M4: Motor_DC; SolderWire-0.1sqmm_1x02_P3.6mm_D0.4mm_OD1mm
Q1, Q2, Q3, Q4: AO3400A; SOT-23_Handsoldering
QR*****: https://github.com/TheScientist101/astra; qrcode
R1, R2: 100k; R_0805_2012Metric_Pad1.20x1.40mm_HandSolder
R3, R6, R7, R10, R11, R20, R21, R23, R24: 10k; R_0805_2012Metric_Pad1.20x1.40mm_HandSolder
R4, R5, R8, R9: 220; R_0805_2012Metric_Pad1.20x1.40mm_HandSolder
R22, R25: 1k; R_0805_2012Metric
SW1, SW2, SW3: SW_Push; SW-SMD_L4.0-W2.9-LS5.0
TP1: TP_BAT; TestPoint_Pad_D2.0mm
TP2: TP_3.3; TestPoint_Pad_D2.0mm
TP3: TP_RST; TestPoint_Pad_D2.0mm
TP4: TP_GND; TestPoint_Pad_D2.0mm
U1: TLV1117LV33DCYR; SOT-223-3_TabPin2
U2: W25Q64JVSSIQ_C179171; SOIC-8_5.3x5.3mm_P1.27mm
U3: STM32H750VBTx; LQFP-100_14x14mm_P0.5mm
U4: BMP388; ST_HLGA-10_2x2mm_P0.5mm_LayoutBorder3x2y
U5: NRF24L01_Breakout; nRF24L01_SMD_Breakout
U7: BMI270; Bosch_LGA-14_3x2.5mm_P0.5mm
U8: HYCW110-TF10-180B; SIM-SMD_HYCW110-TF10-180B
Y1: 25 MHz; Crystal_SMD_3225-4Pin_3.2x2.5mm_HandSoldering

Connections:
+3.3V: C2.1, C6.2, C11.1, C12.1, C13.1, C14.1, C15.1, C22.2, C23.2, C29.1, C30.1, C31.1, C32.1, FB1.1, J2.22, JP1.3 (B), R20.1, R21.1, R23.1, R24.1, TP2.1, U1.2 (VO), U2.8 (VCC), U3.6 (VBAT), U3.11 (VDD), U3.27 (VDD), U3.50 (VDD), U3.75 (VDD), U3.100 (VDD), U4.1 (VDDIO), U4.10 (VDD), U5.2 (VCC), U7.5 (VDDIO), U7.8 (VDD), U8.4 (VDD)
+BATT: C1.2, C18.1, C19.1, C20.1, C21.1, D1.1 (K), D2.1 (K), D3.1 (K), D4.1 (K), D7.1 (VDD), D8.1 (VDD), J1.1, J2.21, J3.1, J4.1, M1.1 (+), M2.1 (+), M3.1 (+), M4.1 (+), R1.2, TP1.1, U1.3 (VI)
BAR_CS: U3.28 (PA4), U4.6 (CSB)
BAT_MEASURE: R1.1, R2.2, U3.32 (PC4)
BOOT: R3.2, U3.94 (BOOT0)
BTN1: SW1.2, U3.25 (PA3)
BTN2: SW3.2, U3.24 (PA2)
DDG_MAGIC_1: J2.11, U3.87 (PD6)
DDG_MAGIC_2: J2.12, U3.86 (PD5)
DDG_MAGIC_3: J2.15, U3.93 (PB7)
DDG_MAGIC_4: J2.16, U3.91 (PB5)
DDG_MAGIC_5: J2.19, U3.98 (PE1)
DDG_MAGIC_6: J2.20, U3.97 (PE0)
DDG_MAGIC_7: J2.9, U3.85 (PD4)
DDG_MAGIC_8: J2.10, U3.84 (PD3)
FLASH_CS: U2.1 (~CS), U3.92 (PB6)
FLASH_IO_0: U2.5 (DI(IO0)), U3.58 (PD11)
FLASH_IO_1: U2.2 (DO(IO1)), U3.59 (PD12)
FLASH_IO_2: U2.3 (WP#(IO2)), U3.1 (PE2)
FLASH_IO_3: U2.7 (HOLD#orRESET#(IO3)), U3.60 (PD13)
FPV_VIN: J4.4, JP2.2 (C)
GND: C1.1, C2.2, C3.2, C4.2, C5.1, C6.1, C7.1, C8.2, C9.1, C10.2, C11.2, C12.2, C13.2, C14.2, C15.2, C16.1, C17.1, C22.1, C23.1, C29.2, C30.2, C31.2, C32.2, D5.1 (K), D6.1 (K), D7.3 (VSS), D8.3 (VSS), J1.2, J2.1, J3.2, J3.MP (MountPin), J4.2, J4.MP (MountPin), JP1.1 (A), Q1.2 (S), Q2.2 (S), Q3.2 (S), Q4.2 (S), R2.1, R6.2, R7.2, R10.2, R11.2, SW1.1, SW2.1, SW3.1, TP4.1, U1.1 (GND), U2.4 (GND), U3.10 (VSS), U3.19 (VSSA), U3.26 (VSS), U3.49 (VSS), U3.74 (VSS), U3.99 (VSS), U4.3 (VSS), U4.8 (VSS), U4.9 (VSS), U5.1 (GND), U7.6 (GNDIO), U7.7 (GND), U8.6 (VSS), U8.10 (CD), U8.11 (EP), U8.12 (EP), Y1.2, Y1.4
HSE_I: C9.2, U3.12 (PH0), Y1.3
HSE_O: C10.1, U3.13 (PH1), Y1.1
I2C1_SCK: J2.18, U3.95 (PB8)
I2C1_SDA: J2.17, U3.96 (PB9)
IMU_CS: U3.45 (PE15), U7.12 (CSB)
IMU_INT1: U3.37 (PE7), U7.4 (INT1)
MOTOR1: R4.1, R6.1, U3.41 (PE11)
MOTOR2: R5.1, R7.1, U3.39 (PE9)
MOTOR3: R8.1, R10.1, U3.69 (PA10)
MOTOR4: R9.1, R11.1, U3.70 (PA11)
NEOPIXEL: D7.4 (DIN), U3.18 (PC3_C)
NRF_CE: U3.46 (PB10), U5.3 (CE)
NRF_CS: U3.47 (PB11), U5.4 (~CSN)
NRF_IRQ: U3.64 (PC7), U5.8 (IRQ)
unnamed: C16.2, C17.2, U3.48 (VCAP), U3.73 (VCAP)
unnamed: C19.2, D1.2 (A), M1.2 (-), Q1.3 (D)
unnamed: C18.2, D2.2 (A), M2.2 (-), Q2.3 (D)
unnamed: C20.2, D3.2 (A), M3.2 (-), Q3.3 (D)
unnamed: C21.2, D4.2 (A), M4.2 (-), Q4.3 (D)
unnamed: D5.2 (A), R22.1
unnamed: D6.2 (A), R25.1
unnamed: D7.2 (DOUT), D8.4 (DIN)
unnamed: JP1.2 (C), R3.1
unnamed: Q1.1 (G), R4.2
unnamed: Q2.1 (G), R5.2
unnamed: Q3.1 (G), R8.2
unnamed: Q4.1 (G), R9.2
unnamed: R24.2, U8.8 (DAT1)
unnamed: R20.2, U8.1 (DAT2)
OSD_VIN: J4.3, JP2.3 (B), U3.57 (PD10)
OSD_VOUT: JP2.1 (A), U3.56 (PD9)
QSPI_CLK: U2.6 (CLK), U3.36 (PB2)
RST: C8.1, J2.8, SW2.2, TP3.1, U3.14 (NRST)
SD_CD: U3.55 (PD8), U8.9 (CD)
SD_CS: U3.51 (PB12), U8.2 (CD/DAT3)
SPI1_CLK: U3.29 (PA5), U4.2 (SCK)
SPI1_MISO: U3.30 (PA6), U4.5 (SDO)
SPI1_MOSI: U3.31 (PA7), U4.4 (SDI)
SPI2_CLK: U3.52 (PB13), U5.5 (SCK), U8.5 (CLK)
SPI2_MISO: R23.2, U3.53 (PB14), U5.7 (MISO), U8.7 (DAT0)
SPI2_MOSI: R21.2, U3.54 (PB15), U5.6 (MOSI), U8.3 (CMD)
SPI3_CLK: J2.5, U3.78 (PC10)
SPI3_MISO: J2.6, U3.79 (PC11)
SPI3_MOSI: J2.7, U3.80 (PC12)
SPI4_MISO: U3.43 (PE13), U7.1 (SDO)
SPI4_MOSI: U3.44 (PE14), U7.14 (SDX)
SPI4_SCK: U3.42 (PE12), U7.13 (SCX)
STATUS_LED_1: R22.2, U3.33 (PC5)
STATUS_LED_2: R25.2, U3.40 (PE10)
TCLK: J2.3, U3.76 (PA14)
TDI: J2.4, U3.77 (PA15)
TDO: J2.14, U3.89 (PB3)
TMS: J2.2, U3.72 (PA13)
TRST: J2.13, U3.90 (PB4)
UART4_RX: J3.3, U3.23 (PA1)
UART4_TX: J3.4, U3.22 (PA0)
VDDA: C3.1, C4.1, C5.2, C7.2, FB1.2, U3.20 (VREF+), U3.21 (VDDA)

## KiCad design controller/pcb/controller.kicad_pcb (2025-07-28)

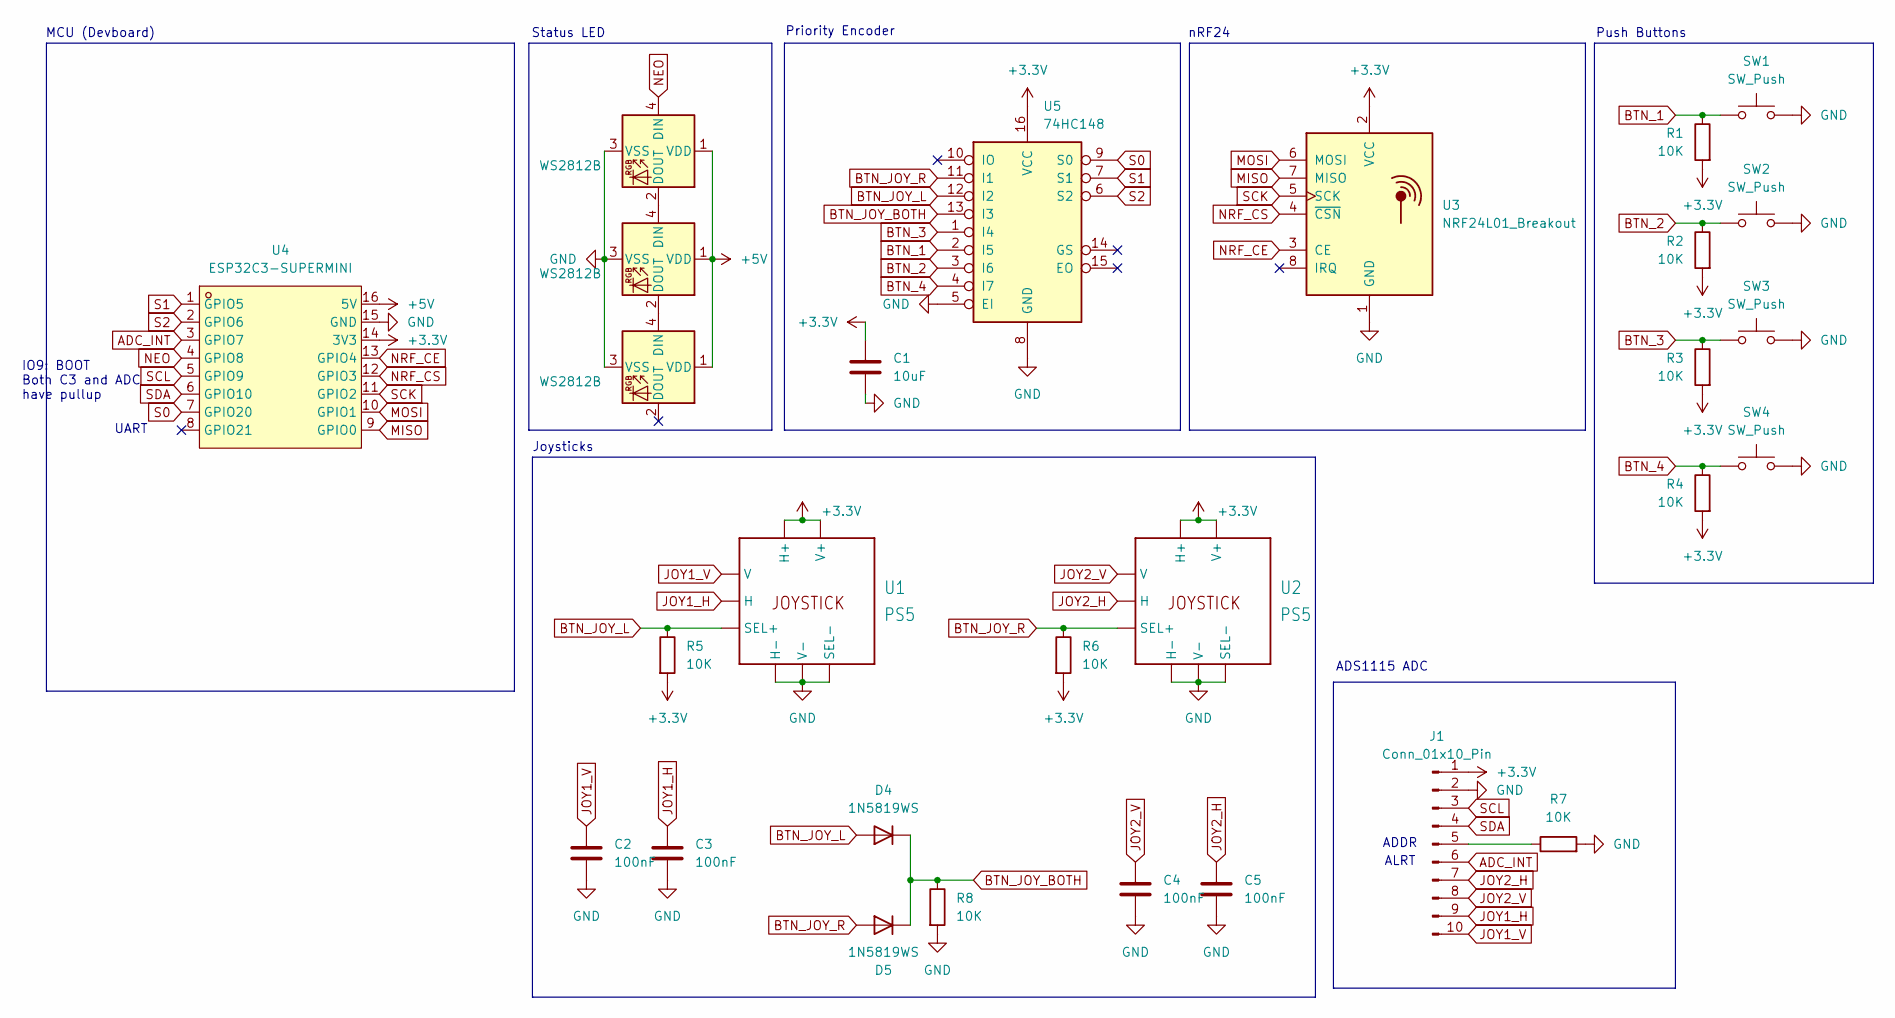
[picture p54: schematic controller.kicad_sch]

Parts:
C1: 10uF; C_0805_2012Metric
C2, C3, C4, C5: 100nF; C_0805_2012Metric
D1, D2, D3: WS2812B; LED_WS2812B_PLCC4_5.0x5.0mm_P3.2mm
D4, D5: 1N5819WS; D_DO-41_SOD81_P7.62mm_Horizontal
J1: Conn_01x10_Pin; PinHeader_1x10_P2.54mm_Vertical
R1, R2, R3, R4, R5, R6, R7, R8: 10K; R_0805_2012Metric
SW1, SW2, SW3, SW4: SW_Push; SW_PUSH-12mm
U1, U2: PS5; Joystick
U3: NRF24L01_Breakout; nRF24L01_SMD_Breakout
U4: ESP32C3-SUPERMINI; ESP32-C3-SuperMini; LCSC Part C9900147397
U5: 74HC148; SOP-16_3.9x9.9mm_P1.27mm

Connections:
+3.3V: C1.1, J1.1, R1.2, R2.2, R3.2, R4.2, R5.2, R6.2, U1.3 (H+), U1.3' (V+), U2.3 (H+), U2.3' (V+), U3.2 (VCC), U4.14 (3V3), U5.16 (VCC)
+5V: D1.1 (VDD), D2.1 (VDD), D3.1 (VDD), U4.16 (5V)
ADC_INT: J1.6, U4.3 (GPIO7)
BTN_1: R1.1, SW1.1, U5.2 (I5)
BTN_2: R2.1, SW2.1, U5.3 (I6)
BTN_3: R3.1, SW3.1, U5.1 (I4)
BTN_4: R4.1, SW4.1, U5.4 (I7)
BTN_JOY_BOTH: D4.1 (K), D5.1 (K), R8.1, U5.13 (I3)
BTN_JOY_L: D4.2 (A), R5.1, U1.a (SEL+), U5.12 (I2)
BTN_JOY_R: D5.2 (A), R6.1, U2.a (SEL+), U5.11 (I1)
GND: C1.2, C2.2, C3.2, C4.2, C5.2, D1.3 (VSS), D2.3 (VSS), D3.3 (VSS), J1.2, R7.2, R8.2, SW1.2, SW2.2, SW3.2, SW4.2, U1.1 (H-), U1.1' (V-), U1.c (SEL-), U2.1 (H-), U2.1' (V-), U2.c (SEL-), U3.1 (GND), U4.15 (GND), U5.5 (EI), U5.8 (GND)
JOY1_H: C3.1, J1.9, U1.2 (H)
JOY1_V: C2.1, J1.10, U1.2' (V)
JOY2_H: C5.1, J1.7, U2.2 (H)
JOY2_V: C4.1, J1.8, U2.2' (V)
MISO: U3.7 (MISO), U4.9 (GPIO0)
MOSI: U3.6 (MOSI), U4.10 (GPIO1)
NEO: D1.4 (DIN), U4.4 (GPIO8)
NRF_CE: U3.3 (CE), U4.13 (GPIO4)
NRF_CS: U3.4 (~CSN), U4.12 (GPIO3)
unnamed: D1.2 (DOUT), D2.4 (DIN)
unnamed: D2.2 (DOUT), D3.4 (DIN)
unnamed: J1.5, R7.1
S0: U4.7 (GPIO20), U5.9 (S0)
S1: U4.1 (GPIO5), U5.7 (S1)
S2: U4.2 (GPIO6), U5.6 (S2)
SCK: U3.5 (SCK), U4.11 (GPIO2)
SCL: J1.3, U4.5 (GPIO9)
SDA: J1.4, U4.6 (GPIO10)

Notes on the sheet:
Joysticks
Status LED
Push Buttons
UART
ALRT
nRF24
Priority Encoder
IO9: BOOT Both C3 and ADC have pullup
ADDR
MCU (Devboard)
ADS1115 ADC

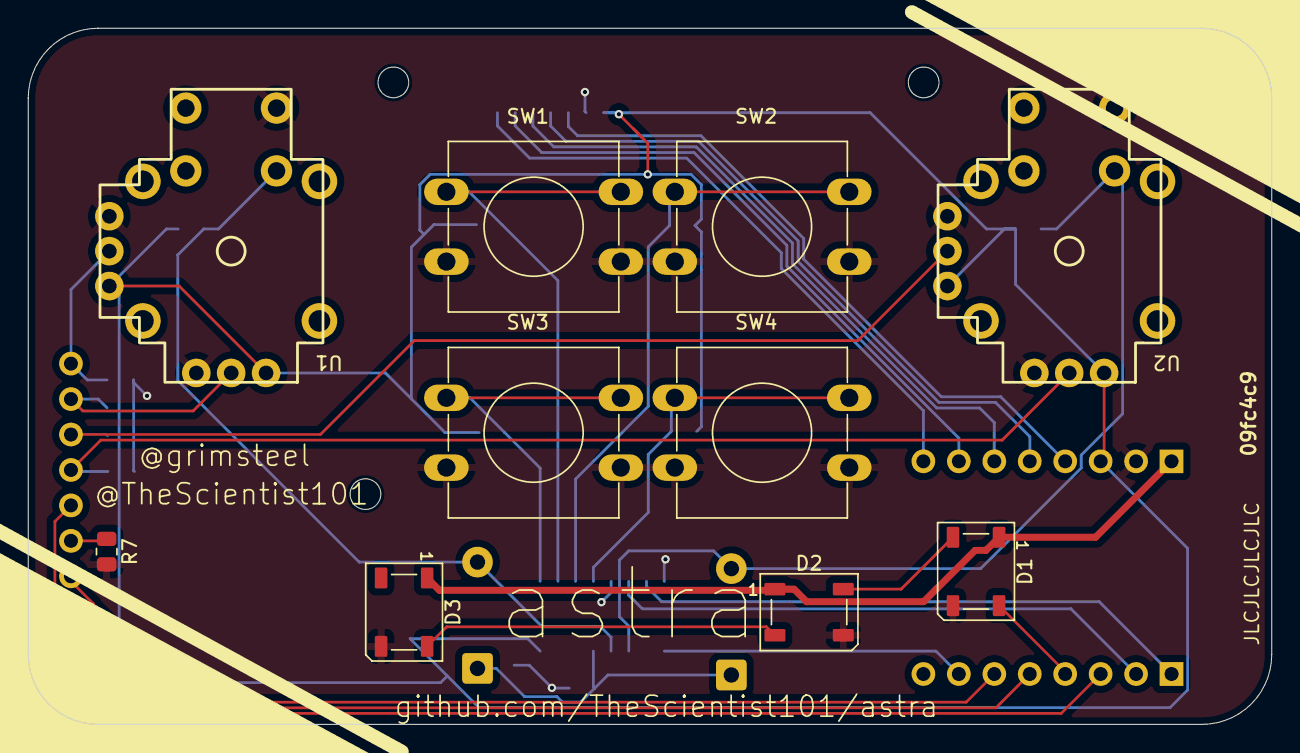
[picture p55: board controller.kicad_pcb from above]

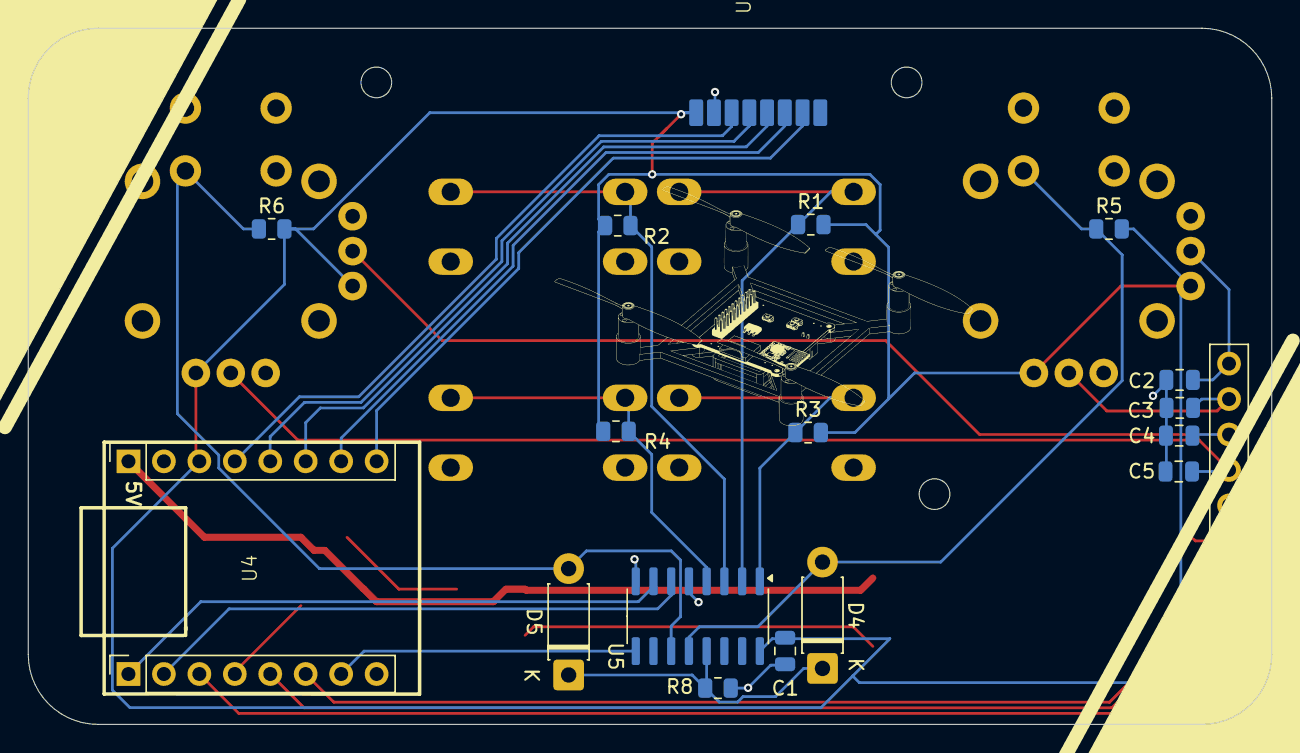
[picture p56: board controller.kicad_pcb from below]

Board: 2 copper layers, 89.1 x 49.9 mm, 28 parts (18 on the bottom side), 29 nets.

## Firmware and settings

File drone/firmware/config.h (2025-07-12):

/*
 * This file is part of Betaflight.
 *
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
 * See the GNU General Public License for more details.
 *
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
 * If not, see <http://www.gnu.org/licenses/>.
 */

#pragma once

#define FC_TARGET_MCU     STM32H750

#define BOARD_NAME        ASTRA
#define MANUFACTURER_ID   DUCK

#define TARGET_BOARD_IDENTIFIER "ASTR"
#define USBD_PRODUCT_STRING "Astra"

#define FC_VMA_ADDRESS    0x97CE0000

#define EEPROM_SIZE 8192

#define USE_SPRACING_PERSISTENT_RTC_WORKAROUND

#define USE_USB_ID

// ======== PERIPHERAL CONFIGURATION =======

#define USE_QUADSPI
#define USE_QUADSPI_DEVICE_1
#define QUADSPI1_SCK_PIN PB2
#define QUADSPI1_BK1_IO0_PIN PD11
#define QUADSPI1_BK1_IO1_PIN PD12
#define QUADSPI1_BK1_IO2_PIN PE2
#define QUADSPI1_BK1_IO3_PIN PD13
#define QUADSPI1_BK1_CS_PIN  PB6
#define QUADSPI1_BK2_IO0_PIN NONE
#define QUADSPI1_BK2_IO1_PIN NONE
#define QUADSPI1_BK2_IO2_PIN NONE
#define QUADSPI1_BK2_IO3_PIN NONE
#define QUADSPI1_BK2_CS_PIN  NONE
#define QUADSPI1_MODE QUADSPI_MODE_BK1_ONLY
#define QUADSPI1_CS_FLAGS (QUADSPI_BK1_CS_HARDWARE | QUADSPI_BK2_CS_NONE | QUADSPI_CS_MODE_LINKED)

// Barometer
#define USE_SPI_DEVICE_1
#define SPI1_SCK_PIN            PA5
#define SPI1_SDI_PIN            PA6
#define SPI1_SDO_PIN            PA7
#define SPI1_NSS_PIN            PA4

// NRF, SD card
#define USE_SPI_DEVICE_2
#define SPI2_SCK_PIN            PB13
#define SPI2_SDI_PIN            PB14
#define SPI2_SDO_PIN            PB15

// DDG
#define USE_SPI_DEVICE_3
#define SPI3_SCK_PIN            PC10
#define SPI3_SDI_PIN            PC11
#define SPI3_SDO_PIN            PC12

// gyro
#define USE_SPI_DEVICE_4
#define SPI4_SCK_PIN            PE12
#define SPI4_SDI_PIN            PE13
#define SPI4_SDO_PIN            PE14

// DDG
#define USE_I2C_DEVICE_1
#define I2C1_SCL_PIN PB8
#define I2C1_SDA_PIN PB9
//  #define I2C_DEVICE I2CDEV_1

// DDG
#define UART2_TX_PIN         PD5
#define UART2_RX_PIN         PD6
#define SERIALRX_UART SERIAL_PORT_USART2

// Standalone JST
#define UART4_TX_PIN         PA0
#define UART4_RX_PIN         PA1

// ======== DEVICE CONFIGURATION ========

// Quad SPI Flash (64 MB)
#define FLASH_QUADSPI_INSTANCE  QUADSPI
#define USE_FLASH
#define USE_FLASH_QUADSPI
#define USE_FLASH_M25P16
#define FLASH_CS_PIN            PB6
#define CONFIG_IN_EXTERNAL_FLASH
#define USE_FIRMWARE_PARTITION

// ADC -  Battery Voltage Measurement
#define USE_ADC
#define ADC_INSTANCE                    ADC1
#define DEFAULT_CURRENT_METER_SOURCE    CURRENT_METER_ADC
//#define DEFAULT_VOLTAGE_METER_SOURCE    VOLTAGE_METER_ADC
//#define DEFAULT_CURRENT_METER_SCALE     100
#define DEFAULT_VOLTAGE_METER_SCALE     110
#define ADC_VBAT_PIN                    PC4
//#define ADC_RSSI_PIN         PC4
//#define ADC_CURR_PIN         PC0
//#define ADC_EXTERNAL1_PIN    PC5
//#define DEFAULT_FEATURES FEATURE_RSSI_ADC

// MicroSD Card - SPI2
#define USE_SDCARD
#define USE_SDCARD_SPI
#define SDCARD_SPI_CS_PIN    PB12
#define SDCARD_DETECT_PIN    PD8
#define SDCARD_DETECT_INVERTED
#define DEFAULT_BLACKBOX_DEVICE BLACKBOX_DEVICE_SDCARD
#define SDCARD_SPI_INSTANCE  SPI2

// Barometer - SPI1
#define USE_BARO
#define USE_BARO_BMP388
#define BARO_SPI_INSTANCE    SPI1
#define BARO_CS_PIN          PA4

// WS2812B
#define USE_LED_STRIP
#define LED_STRIP_PIN        PC3

// Motors - PWM TIM1
#define MOTOR1_PIN           PE9
#define MOTOR2_PIN           PE11
#define MOTOR3_PIN           PA10
#define MOTOR4_PIN           PA11

// RX - NRF24
#define USE_RX
#define USE_RX_NRF24
#define USE_RX_SPI
// protocol - can be customized
#define USE_RX_SYMA
#define RX_CE_PIN           PB10
#define RX_SPI_CS_PIN       PB11
#define RX_SPI_EXTI_PIN     PC7
#define RX_SPI_INSTANCE     SPI2
#define RX_NSS_PIN          RX_SPI_CS_PIN

// BMI270 - SPI4
#define USE_GYRO
#define USE_ACC
#define USE_ACCGYRO_BMI270
#define GYRO_1_EXTI_PIN      PE14
#define GYRO_1_SPI_INSTANCE  SPI4
#define GYRO_1_ALIGN         CW0_DEG_FLIP
#define GYRO_1_CS_PIN        PE7

// Status LEDs
#define LED0_PIN             PC5
#define LED1_PIN             PE10

// Custom Buttons
#define USE_BUTTONS
#define BUTTON_A_PIN            PA3
#define BUTTON_A_PIN_INVERTED
#define BUTTON_B_PIN            PA2
#define BUTTON_B_PIN_INVERTED

// ========= DMA CONFIGURATION =========

// TODO: figure out these once we get the board
#define ADC1_DMA_OPT            8
#define TIMUP1_DMA_OPT          0
#define TIMUP2_DMA_OPT          0
#define TIMUP3_DMA_OPT          0
#define TIMUP4_DMA_OPT          0
#define TIMUP5_DMA_OPT          0
#define TIMUP8_DMA_OPT          2

#define TIMER_PIN_MAPPING \
    TIMER_PIN_MAP(0, PA8, 1, 10) \
    TIMER_PIN_MAP(1, PB11, 1, 11) \
    TIMER_PIN_MAP(2, PB15, 2, -1) \
    TIMER_PIN_MAP(3, PE5, 1, 0) \
    TIMER_PIN_MAP(4, PE6, 1, -1) \
    TIMER_PIN_MAP(5, PA0, 2, 0) \
    TIMER_PIN_MAP(6, PA1, 2, 1) \
    TIMER_PIN_MAP(7, PA2, 2, 2) \
    TIMER_PIN_MAP(8, PA3, 2, 3) \
    TIMER_PIN_MAP(9, PB6, 2, 4) \
    TIMER_PIN_MAP(10, PB7, 2, 5) \
    TIMER_PIN_MAP(11, PC6, 2, 6) \
    TIMER_PIN_MAP(12, PC7, 2, 7) \
    TIMER_PIN_MAP(13, PD14, 1, 12) \
    TIMER_PIN_MAP(14, PD15, 1, -1) \
    TIMER_PIN_MAP(15, PA6, 1, 0) \
    TIMER_PIN_MAP(16, PA7, 2, 0) \
    TIMER_PIN_MAP(17, PB0, 2, 0) \
    TIMER_PIN_MAP(18, PB1, 2, 0)

#define TIMUP1_DMA_OPT 0
#define TIMUP2_DMA_OPT 0
#define TIMUP3_DMA_OPT 0
#define TIMUP4_DMA_OPT 0
#define TIMUP5_DMA_OPT 0
#define TIMUP8_DMA_OPT 2

// FPV stuff

//#define USE_MAX7456
//#define CAMERA_CONTROL_PIN   PE5
//#define MAX7456_SPI_CS_PIN   PE11
//#define MAX7456_SPI_INSTANCE SPI4

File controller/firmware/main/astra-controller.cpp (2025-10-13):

#include <esp_timer.h>
#include <freertos/FreeRTOS.h>
#include <freertos/timers.h>
#include <driver/gpio.h>
#include <esp_log.h>
#include "led_strip.h"
#include "led_strip_types.h"
#include "i2cdev.h"
#include "v202_protocol.hpp"
#include "nrf24.hpp"
#include "joystick.hpp"

#define NEOPIXEL_GPIO GPIO_NUM_8
#define NUM_NEOPIXEL 3

// this is a UART pin - might need to be disabled
#define BUTTON_ENCODER_0 GPIO_NUM_20
#define BUTTON_ENCODER_1 GPIO_NUM_5
#define BUTTON_ENCODER_2 GPIO_NUM_6

#define ADC_SDA GPIO_NUM_10
#define ADC_SCL GPIO_NUM_9
#define ADC_INT GPIO_NUM_7

typedef enum {
  BTN_NONE = 0,
  BTN_JOY_R = 1,
  BTN_JOY_L = 2,
  BTN_JOY_BOTH = 3,
  BTN_3 = 4,
  BTN_1 = 5,
  BTN_2 = 6,
  BTN_4 = 7
} button_state_t;

// this essentially stores the currently pressed button number (1-7)
static button_state_t button_state = BTN_NONE;

/// Higher-level handler for buttons presses
static void button_press_handler(button_state_t button_pressed) {
  // TODO: unimplemented
  // note - this is called from an interrupt - use queues if delays or other long operations are needed
}

/// Button priority encoder interrupt handler
static void IRAM_ATTR button_isr_handler(void* arg) {
  gpio_num_t gpio_num = (gpio_num_t) (uint32_t) arg;
  // active-low, so invert
  int new_pin_state = !gpio_get_level(gpio_num);
  uint8_t new_button_state = button_state;

  // convert gpio number to bit index
  uint8_t bit;
  switch (gpio_num) {
    case BUTTON_ENCODER_0:
      bit = 0; break;
    case BUTTON_ENCODER_1:
      bit = 1; break;
    case BUTTON_ENCODER_2:
      bit = 2; break;
    default: return;
  }

  // clear
  new_button_state &= ~(1 << bit);
  // set
  new_button_state |= (new_pin_state << bit);

  if (new_button_state != button_state) {
    button_press_handler(button_state = (button_state_t) new_button_state);
  }
}

led_strip_handle_t init_neopixel() {
  // configure neopixel
  led_strip_config_t neopixel_config = {
    .strip_gpio_num = NEOPIXEL_GPIO,
    .max_leds = NUM_NEOPIXEL,
    .led_model = LED_MODEL_WS2812,
    .color_component_format = LED_STRIP_COLOR_COMPONENT_FMT_GRB,
    .flags = {
      .invert_out = false
    }
  };
  led_strip_rmt_config_t neopixel_rmt_config = {
    .clk_src = RMT_CLK_SRC_DEFAULT,
    .resolution_hz = 10 * 1000 * 1000, // 10 MHz
    .mem_block_symbols = 64,
    .flags = {
      .with_dma = false, // not available on C3
    }
  };
  led_strip_handle_t neopixel_handle = nullptr;
  ESP_ERROR_CHECK(led_strip_new_rmt_device(&neopixel_config, &neopixel_rmt_config, &neopixel_handle));
  // turn all off
  led_strip_clear(neopixel_handle);
  return neopixel_handle;
}

void init_buttons() {
  // configure button GPIOs
  gpio_config_t io_conf = {
    // rising or falling
    .pin_bit_mask = (1ULL << BUTTON_ENCODER_0) | (1ULL << BUTTON_ENCODER_1) | (1ULL << BUTTON_ENCODER_2),
    .mode = GPIO_MODE_INPUT,
    .pull_up_en = GPIO_PULLUP_ENABLE,
    .pull_down_en = GPIO_PULLDOWN_DISABLE,
    .intr_type = GPIO_INTR_ANYEDGE,
  };
  gpio_config(&io_conf);

  // register interrupt handlers
  gpio_isr_handler_add(BUTTON_ENCODER_0, button_isr_handler, (void*) BUTTON_ENCODER_0);
  gpio_isr_handler_add(BUTTON_ENCODER_1, button_isr_handler, (void*) BUTTON_ENCODER_1);
  gpio_isr_handler_add(BUTTON_ENCODER_2, button_isr_handler, (void*) BUTTON_ENCODER_2);
}

uint8_t map_v202_rotation(uint8_t joystick_value) {
  int8_t signed_value = (int8_t) (joystick_value - 128);

  // [-128, 0] gets mapped to [0, 128] (left)
  if (signed_value <= 0) return (uint8_t) (-signed_value);
  // (0, 127] gets mapped to (128, 255] (right)
  else return (uint8_t) (signed_value) + 0x80;
}

extern "C" void app_main(void)
{
  // setup per-pin interrupts
  ESP_ERROR_CHECK(gpio_install_isr_service(0));

  TaskHandle_t main_task = xTaskGetCurrentTaskHandle();

  led_strip_handle_t neopixel = init_neopixel();
  // LED 0 <- Red
  ESP_ERROR_CHECK(led_strip_set_pixel(neopixel, 0, 15, 0, 0));
  ESP_ERROR_CHECK(led_strip_set_pixel(neopixel, 1, 0, 16, 0));
  ESP_ERROR_CHECK(led_strip_set_pixel(neopixel, 2, 0, 0, 15));
  led_strip_refresh(neopixel);

  init_buttons();

  // configure TX
  V202 v202;
  // pins configured in defconfig
  NRF24 nrf24;
  v202.init(&nrf24, TX, TAER);
  uint8_t id[] = {0,0,0};
  v202.setTXId(id);
  
  ESP_ERROR_CHECK(i2cdev_init());

  // initialize joystick ADC
  Joystick joystick(ADC_SDA, ADC_SCL, ADC_INT);

  // start joystick main loop
  joystick.start(main_task);

  // wait for initialization
  ulTaskNotifyTakeIndexed(JOYSTICK_TASK_NOTIFY_INDEX, pdTRUE, portMAX_DELAY);

  // main loop
  while (true) {
    // transmitter mode 2
    uint8_t throttle = joystick.joy1_v;
    uint8_t yaw = map_v202_rotation(joystick.joy1_h);
    uint8_t pitch = map_v202_rotation(joystick.joy2_v);
    uint8_t roll = map_v202_rotation(joystick.joy2_h);

    ESP_LOGI("HI", "%d %d %d %d %d", throttle, yaw, pitch, roll, button_state);

    // TODO: do something here
    uint8_t flags = 0;
    v202.command(throttle, yaw, pitch, roll, flags);

    ESP_LOGI("HI", "send");

    vTaskDelay(1000 / portTICK_PERIOD_MS);
  }
}

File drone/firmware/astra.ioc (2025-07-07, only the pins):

Mcu.UserName=STM32H750VBTx
PA0.GPIO_Label=DDG_MAGIC_2
PA0.Signal=GPIO_Output
PA1.GPIO_Label=DDG_MAGIC_3
PA1.Signal=GPIO_Output
PA10.Signal=S_TIM1_CH3
PA11.Signal=S_TIM1_CH4
PA2.GPIO_Label=DDG_MAGIC_4
PA2.Signal=GPIO_Output
PA3.GPIO_Label=DDG_MAGIC_5
PA3.Signal=GPIO_Output
PA4.Signal=DCMI_HSYNC
PA6.Signal=DCMI_PIXCLK
PA7.GPIO_Label=STATUS_LED
PA7.Signal=GPIO_Output
PA9.Signal=DCMI_D0
PB10.Signal=I2C2_SCL
PB11.Signal=I2C2_SDA
PB12.GPIO_Label=SD_CS
PB12.Signal=SPI2_NSS
PB13.Signal=SPI2_SCK
PB14.Signal=SPI2_MISO
PB15.Signal=SPI2_MOSI
PB2.Signal=QUADSPI_CLK
PB6.Signal=QUADSPI_BK1_NCS
PB7.Signal=DCMI_VSYNC
PB8.Signal=I2C1_SCL
PB9.Signal=I2C1_SDA
PC10.Signal=DCMI_D8
PC11.Signal=DCMI_D4
PC12.Signal=DCMI_D9
PC3_C.GPIO_Label=DDG_MAGIC_1
PC3_C.Signal=GPIO_Output
PC4.GPIO_Label=BAT_MEASURE
PC4.Signal=ADCx_INP4
PC7.Signal=DCMI_D1
PD11.Signal=QUADSPI_BK1_IO0
PD12.Signal=QUADSPI_BK1_IO1
PD13.Signal=QUADSPI_BK1_IO3
PD3.Signal=DCMI_D5
PD6.GPIO_Label=DCMI_PWDN
PD6.Signal=GPIO_Output
PD7.GPIO_Label=DCMI_RST
PD7.Signal=GPIO_Output
PE0.Signal=DCMI_D2
PE1.Signal=DCMI_D3
PE11.Signal=S_TIM1_CH2
PE12.GPIO_Label=NRF_CS
PE12.Signal=GPIO_Output
PE13.GPIO_Label=NRF_CE
PE13.Signal=GPIO_Output
PE2.Signal=QUADSPI_BK1_IO2
PE5.Signal=DCMI_D6
PE6.Signal=DCMI_D7
PE9.Signal=S_TIM1_CH1

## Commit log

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2025-06-11 [pcb] Started STM32 schematic
    [mcu.kicad_sch]
2025-06-11 [journal] add 6/10 schematic entry
    [astra.kicad_sch, motor-controller.kicad_sch]
2025-06-11 [pcb] More STM32 power
    [mcu.kicad_sch]
2025-06-11 [pcb] initial motor controller
    [motor-controller.kicad_sch]
2025-06-13 [pcb] start transceiver implementation
    [astra.kicad_sch, mcu.kicad_sch, peripherals.kicad_sch]
2025-06-13 [pcb] motor controllers, label/group cleanup
    [mcu.kicad_sch, motor-controller.kicad_sch, peripherals.kicad_sch]
2025-06-13 [pcb] improve MCU analog power, battery voltage measurement, JTAG header
    [mcu.kicad_sch, peripherals.kicad_sch]
2025-06-14 [pcb] gpio selection, camera, crystal
    - Each motors is connected to a channel of TIM1
    - The battery voltage divider is connected to ADC1
    - The NRF24 is connected to SPI2
    - Added OV5640 camera (FPC connector) + LDOs
    [mcu.kicad_sch, motor-controller.kicad_sch, peripherals.kicad_sch]
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2025-06-16 [bom] pcb components and [pcb] assign footprints
    [mcu.kicad_sch, motor-controller.kicad_sch, peripherals.kicad_sch]
2025-06-19 [pcb] initial layout and power routing
    [astra.kicad_pcb, mcu.kicad_sch, peripherals.kicad_sch]
2025-06-20 [pcb] and [bom] add micro secure digital card interface socket connector
    [mcu.kicad_sch, peripherals.kicad_sch]
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2025-06-22 [pcb] 4 layer routing
    [astra.kicad_pcb]
2025-06-30 [pcb] continue routing - motors, camera, battery
    [astra.kicad_pcb, mcu.kicad_sch, peripherals.kicad_sch]
2025-07-01 [pcb] invented the cutting edge, extremely innovative monke and ddg connectors
    [mcu.kicad_sch, peripherals.kicad_sch]
2025-07-01 [pcb] changed switches to optimize pcb layout
    [astra.kicad_pcb, mcu.kicad_sch, peripherals.kicad_sch]
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2025-07-03 [pcb] add some 3d mooodels
    [astra.kicad_pcb, motor-controller.kicad_sch]
2025-07-05 [pcb] controller schematic, intial layout
    [astra.kicad_pcb, controller.kicad_pcb, controller.kicad_sch]
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2025-07-06 [pcb] silkscreen labels and logos
    [astra.kicad_pcb]
2025-07-07 [pcb] add status led
    [astra.kicad_pcb, mcu.kicad_sch, peripherals.kicad_sch]
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2025-07-07 [pcb] small fixes and improvements
    - add two status LEDs
    - move silkscreen labels for better visibility
    - add more silkcreen logos/credits
    - fix nrf footprint, add rf keepout zone
    - add mounting holes
    [astra.kicad_pcb, mcu.kicad_sch, peripherals.kicad_sch]
2025-07-09 [pcb] remove on-board camera
    - remove camera and all supporting components (we'll be using an external dedicated board)
    - extend DDG header
    - make PCB smaller
    - add more silkscreen labels
    [astra.kicad_pcb, mcu.kicad_sch, peripherals.kicad_sch]
2025-07-09 [pcb] utilize unused gpios, silkscreen improvements and [journal] add entry for 7/9
    [astra.kicad_pcb, mcu.kicad_sch, peripherals.kicad_sch]
2025-07-10 [pcb] some more silkscreen improvements
    [astra.kicad_pcb, peripherals.kicad_sch]
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2025-07-10 [pcb] switch bmi270 to SPI, wire interrupt pins and SD chip detect
    [astra.kicad_pcb, mcu.kicad_sch, peripherals.kicad_sch]
2025-07-12 [firmware] add nRF24 RX config
    [astra.kicad_pcb]
2025-07-13 [pcb] change pico for c3 supermini and use priority encoder for more inputs
    [controller.kicad_pcb, controller.kicad_sch]
2025-07-13 [pcb] dogbone board edge for mounting holes
    [astra.kicad_pcb]
2025-07-13 [pcb] finish controller schematic, route controller pcb
    [controller.kicad_pcb, controller.kicad_sch]
2025-07-15 [pcb] various routing improvements
    [astra.kicad_pcb, mcu.kicad_sch]
2025-07-15 [pcb] reroute front traces under stm32
    [astra.kicad_pcb]
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2025-07-19 [firmware] add v202 protocl and nrf24 driver code
    [controller.kicad_pcb, controller.kicad_sch]
2025-07-19 [controller] add smoothing caps to ADC lines
    [controller.kicad_pcb, controller.kicad_sch]
2025-07-19 [controller] use higher quality external ADC
    [controller.kicad_pcb, controller.kicad_sch]
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2025-07-20 [controller] finish firmware, implement better ADC sampling w/ interrupt
    [controller.kicad_pcb, controller.kicad_sch]
2025-07-20 [controller] fix firmware linking issues
    [astra-controller.cpp, joystick.cpp]
2025-07-21 [pcb] add JST FPV connector
    [astra.kicad_pcb, mcu.kicad_sch, peripherals.kicad_sch]
2025-07-21 [bom] change battery and [controller] add button 3d files
    [astra.kicad_pcb, controller.kicad_pcb, controller.kicad_sch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]
2025-07-21 [cad] add drone cad files
    [battery-mount.step, frame.step]
2025-07-21 [pcb] add production files
    [bom.csv, designators.csv, positions.csv]
2025-07-21 [pcb] change footprint for joystick on controller
    [controller.kicad_pcb, controller.kicad_sch]
2025-07-21 [cad] design controller case
    [assembled.scad, basics.scad, case_bottom.scad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]
2025-07-21 [pcb] update battery connector footprint
    [astra.kicad_pcb, bom.csv, mcu.kicad_sch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]
2025-07-21 [pcb] add additional mounting hole for controller
    [controller.kicad_pcb]
2025-07-21 [cad] add additional mounting hole for controller
    [assembled.scad, case_bottom.scad, case_top.scad]
2025-07-21 [journal] update journal entry for 07/20
    [assembled.scad]
2025-07-21 [bom] add bom CSV, fix quantities
    [BOM.csv]
2025-07-21 [docs] add controller photos and "why" to readme
    [controller.kicad_pcb, controller.kicad_sch]
2025-07-21 [bom] tax + shipping and [controller] add silkscreen
    [BOM.csv, controller.kicad_pcb]
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2025-07-28 [bom] replace solder paste and m2 set with cheaper alternative
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2025-10-13 [controller] firmware updates and fixes
    [spacer.scad]
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2025-10-13 [pcb] drc fixes
    [astra-v2.kicad_pcb, mcu.kicad_sch]
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

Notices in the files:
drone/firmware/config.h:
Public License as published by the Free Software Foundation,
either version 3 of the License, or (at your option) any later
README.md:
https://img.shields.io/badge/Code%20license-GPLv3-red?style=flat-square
